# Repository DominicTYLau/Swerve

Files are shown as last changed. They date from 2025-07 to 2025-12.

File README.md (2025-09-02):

# Swerve

**Description:

** A swerve drivetrain completely 3D printed.

**Motivation for this project:** I wanted to make something similar to FRC swerve. I want to learn to program it.

Full CAD: https://a360.co/44cCmrA

## Demo:
https://youtube.com/shorts/nQBawvd5q3g?feature=share

## Pictures:
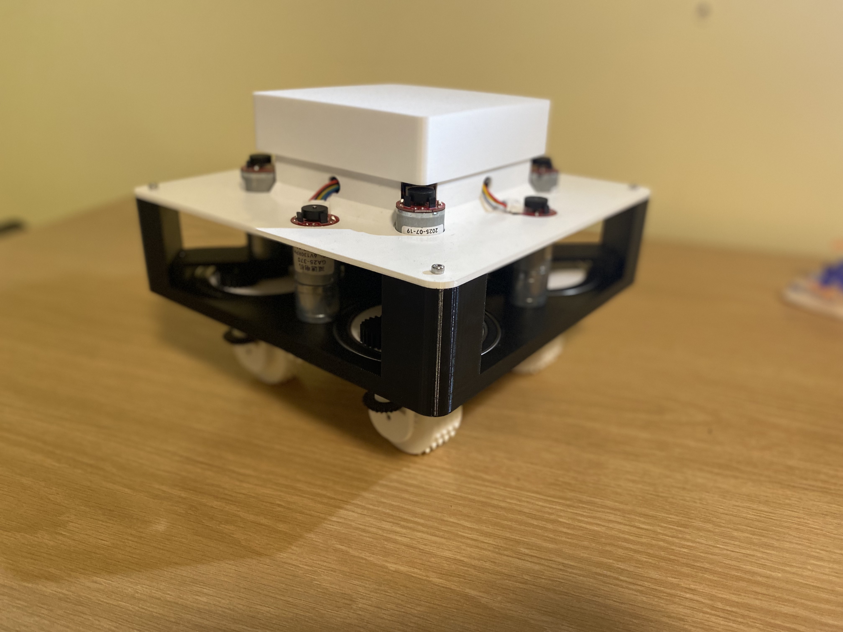
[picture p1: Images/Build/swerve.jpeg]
Swerve


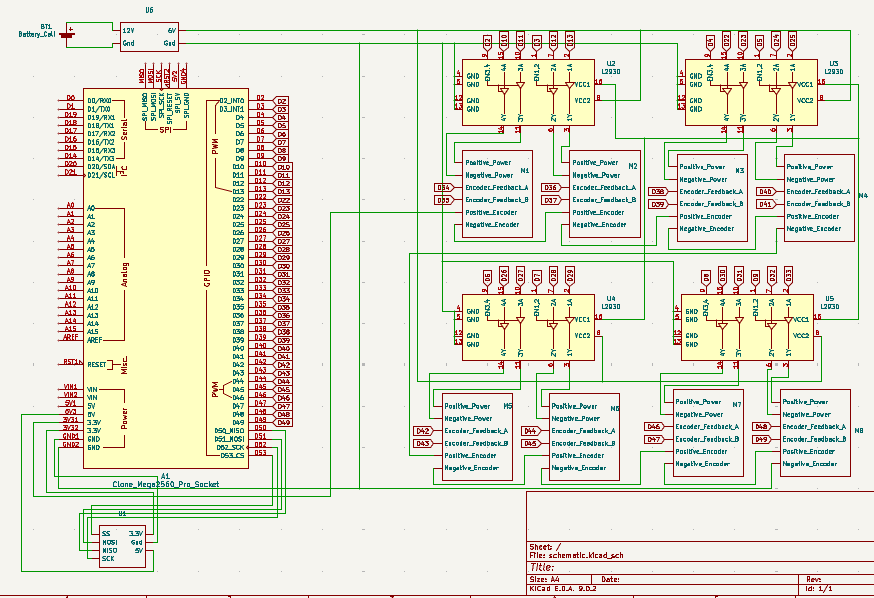
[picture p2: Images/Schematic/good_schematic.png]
Schematic


## BOM:

Purchase Items

| Item Name | What the Item Is For in Your Project | Item Source | Item Price (USD) | Quantity | Total Price (USD) | URL |
|---|---|---|---|---|---|-----|
| Geared Motors w/ encoders | One for steering motor and the other for drive motor. Four Wheels. | Aliexpress  | 10.93 | 8 | 87.44 | [Link](https://www.aliexpress.com/item/4001314473291.html) |
| M4 - 45 Hex Head Bolts | Transfer in power (check CAD) | Aliexpress  | 2.81 | 1 | 2.81 | [Link](https://www.aliexpress.com/item/32968601031.html) |
| Bearings | For rotation of each module | Aliexpress  | 13.29 | 2 | 26.58 | [Link](https://www.aliexpress.com/item/1005007420073930.html) |
| Arduino Mega | Need more ports | Amazon | 23.10 | 1 | 23.10 | [Link](https://www.amazon.ca/dp/B01H4ZLZLQ) |

**Total:** $149.96 USD

## Already Have

| Item | What the Item Is For in Your Project | Source  | Quantity | URL |
|---|---|---|---|-----|
| Lipo Battery | Power Robot | Amazon  | 1 | — |
| L293D | Motor Driver | Amazon  | 4 | — |
| M3 - 8mm Bolts  | — | Aliexpress | 1 | [Link](https://www.aliexpress.com/item/32810872544.html) |
| M4 - 40mm Bolts | — | Aliexpress | 1 | [Link](https://www.aliexpress.com/item/32810872544.html) |
| M3 - 4mm Bolts  | — | Aliexpress | 1 | [Link](https://www.aliexpress.com/item/32810872544.html) |
| ESP32  | — | Amazon | 1 | - |

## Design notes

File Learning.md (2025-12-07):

Each project allows me to grow. For this project, I learned:

* That the design and CAD phase is very important, as it saves a lot of time later on when building.
* To 3D print test pieces to avoid parts that don’t fit.
* To place the pinouts on the microcontroller near where they will be connected, making it easier to troubleshoot.
* That it is important to ensure the motors are receiving enough current.

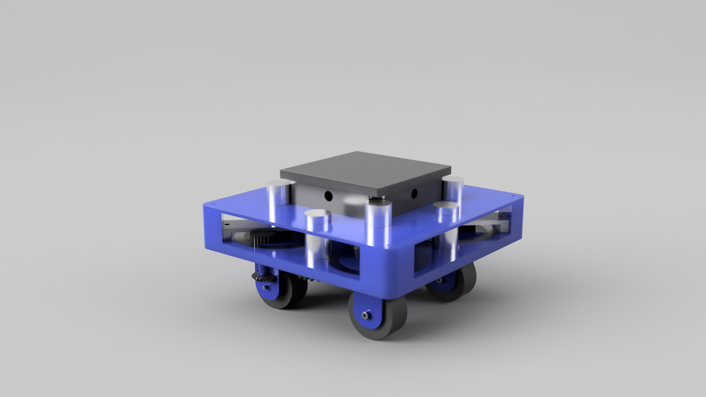
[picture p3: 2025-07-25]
Images/render.png

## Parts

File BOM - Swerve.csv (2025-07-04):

 |  |  |  | USD
Item name | What the item is for in your project | Item source | Item price (include taxes) | Quantity | Total Price (include shipping + taxes) | URL
Geared Motors w/ encoders | One for steering motor and the other for drive motor. Four Wheels. | Aliexpress | 10.93 | 8 | 87.44 | https://www.aliexpress.com/item/4001314473291.html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
Bluetooth Dongle | Connect game controller to control robot | Amazon | 2.77 | 1 | 2.77 | https://www.aliexpress.com/item/1005007299146273.html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
USB Host Shield | Connect USB to Arduino | Aliexpress | 4.34 | 1 | 4.34 | https://www.aliexpress.com/item/32817563853.html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 | Reference --> | https://www.amazon.ca/HiLetgo-Development-Compatible-Interface-Arduino/dp/B01EWW9R1E
IC Socket | Place for L293D to be placed so they can be resuable | Aliexpress | 2.92 | 1 | 2.92 | https://www.aliexpress.com/item/32863286734.html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
M4 - 45 Hex Head Bolts | To transfer power (check CAD) | Aliexpress | 2.81 | 1 | 2.81 | https://www.aliexpress.com/item/32968601031.html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
Bearings | For rotation of each module | Aliexpress | 13.29 | 2 | 26.58 | https://www.aliexpress.com/item/1005007420073930.html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
Arduino Mega | Need more ports | Amazon | 23.1 | 1 | 23.1 | https://www.amazon.ca/ELEGOO-Compatible-Arduino-Projects-Compliant/dp/B01H4ZLZLQ?s=industrial
 |  |  |  |  | 149.96
Already Have
Lipo Battery | Power Robot | Amazon
L293D | Motor Driver | Amazon
M3 - 8mm Bolts |  | Aliexpress | 2.36 | 1 | 2.36 | https://www.aliexpress.com/item/32810872544.html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
M4 - 40mm Bolts |  | Aliexpress | 4.34 | 1 | 4.34 | https://www.aliexpress.com/item/32810872544.html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
M3 - 4mm Bolts |  | Aliexpress | 1.94 | 1 | 1.94 | https://www.aliexpress.com/item/32810872544.html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

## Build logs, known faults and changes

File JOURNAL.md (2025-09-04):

---
title: "Swerve Bot"
author: "Dominic Lau"
description: "A swerve drivetrain that is 3D printed"
created_at: "2024-06-23"
---

Time Spent: 52 hours

# Planning & Designing

---

## June 23, 2025

New idea. Create a swerve drive that had odometry. I started by drawing different designs to see which ones were possible. I then did a simple cad to test if it would work. The cad took the longest because I had to figure out the best dimensions.

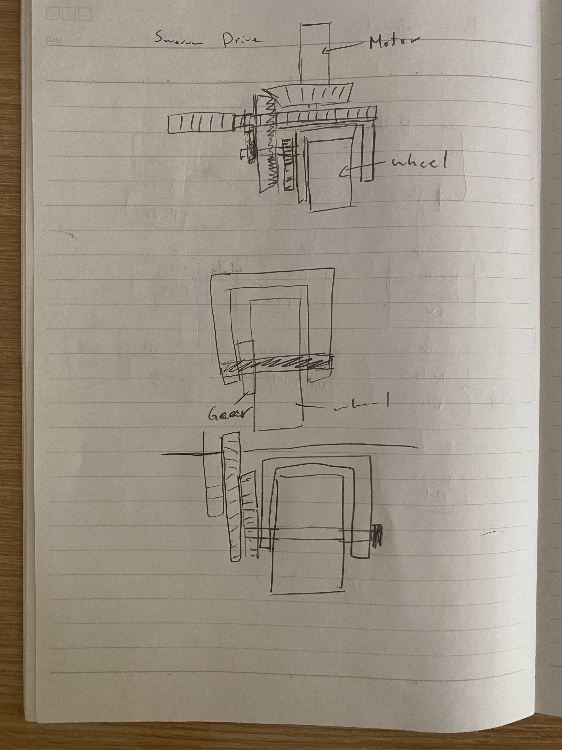
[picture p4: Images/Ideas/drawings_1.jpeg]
drawings_1

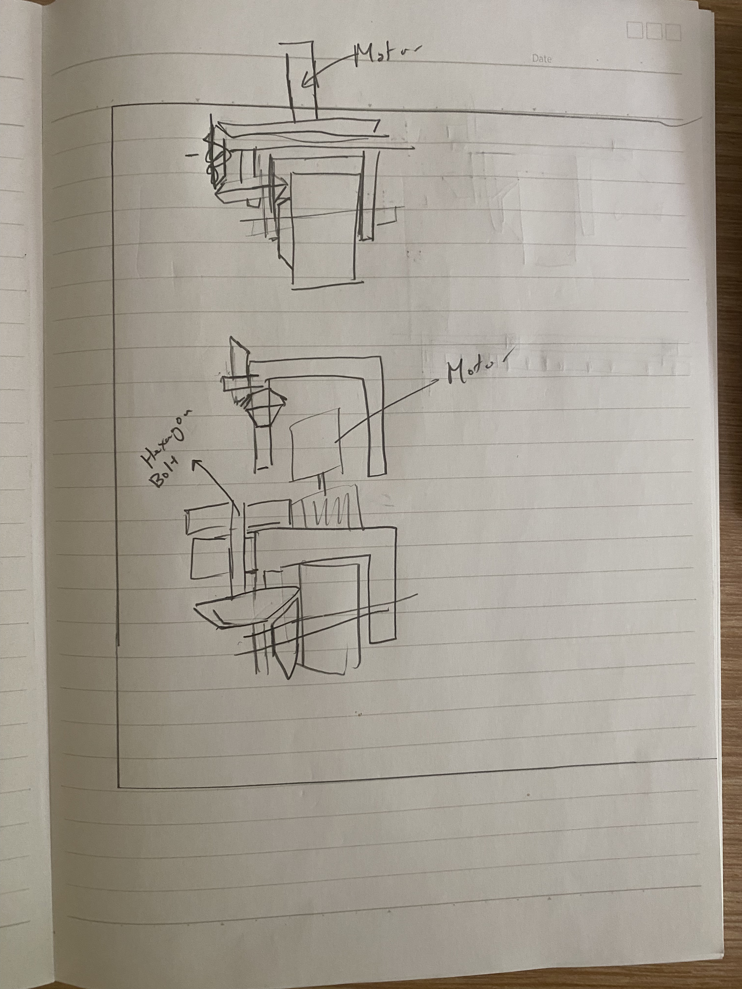
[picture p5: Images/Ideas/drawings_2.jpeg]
drawings_2

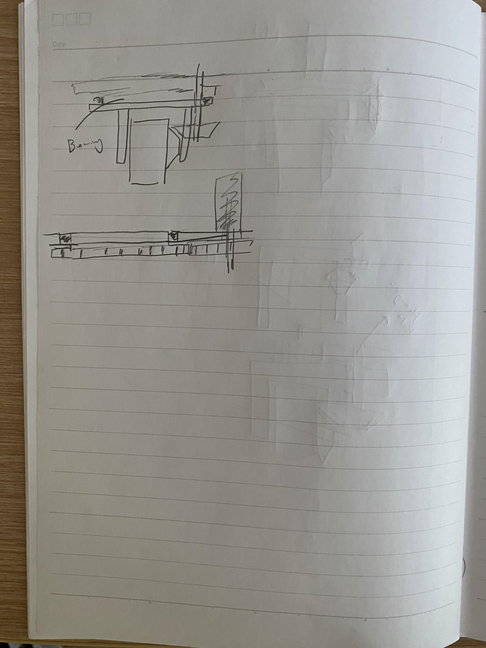
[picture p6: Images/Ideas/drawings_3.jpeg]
drawings_3


Time Spent: 1 hour

## June 24, 2025

I assembled the prototype. It worked pretty well. I had to fix some dimensions in the cad. I caded a bigger prototype that had more gears. I basically made one module of the swerve drivetrain. I also researched about the motors I was going to use. I wanted to have encoder to be more precise.

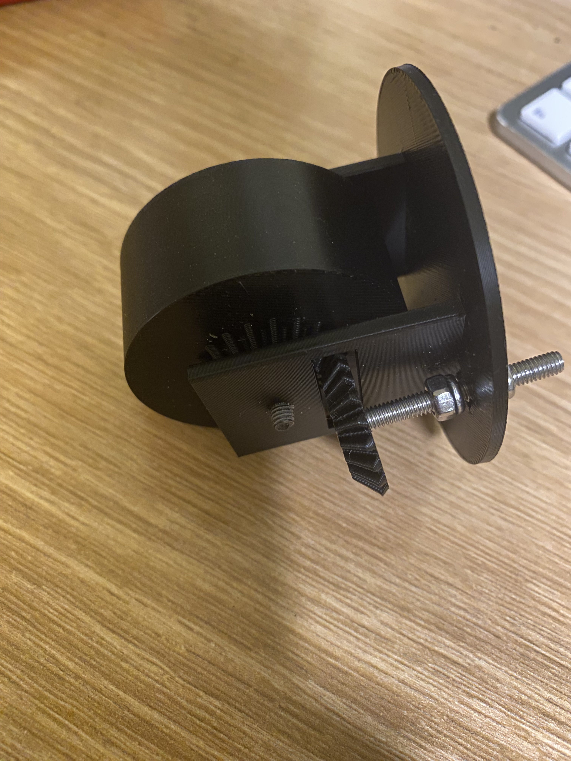
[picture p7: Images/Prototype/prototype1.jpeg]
prototype1


Time Spent: 2 hours

## June 25, 2025

I tested the second prototype and it worked pretty well. I spent the day cadding the whole robot. It took a lot of time trying to get all the joints working. The animations work and it looks pretty cool.

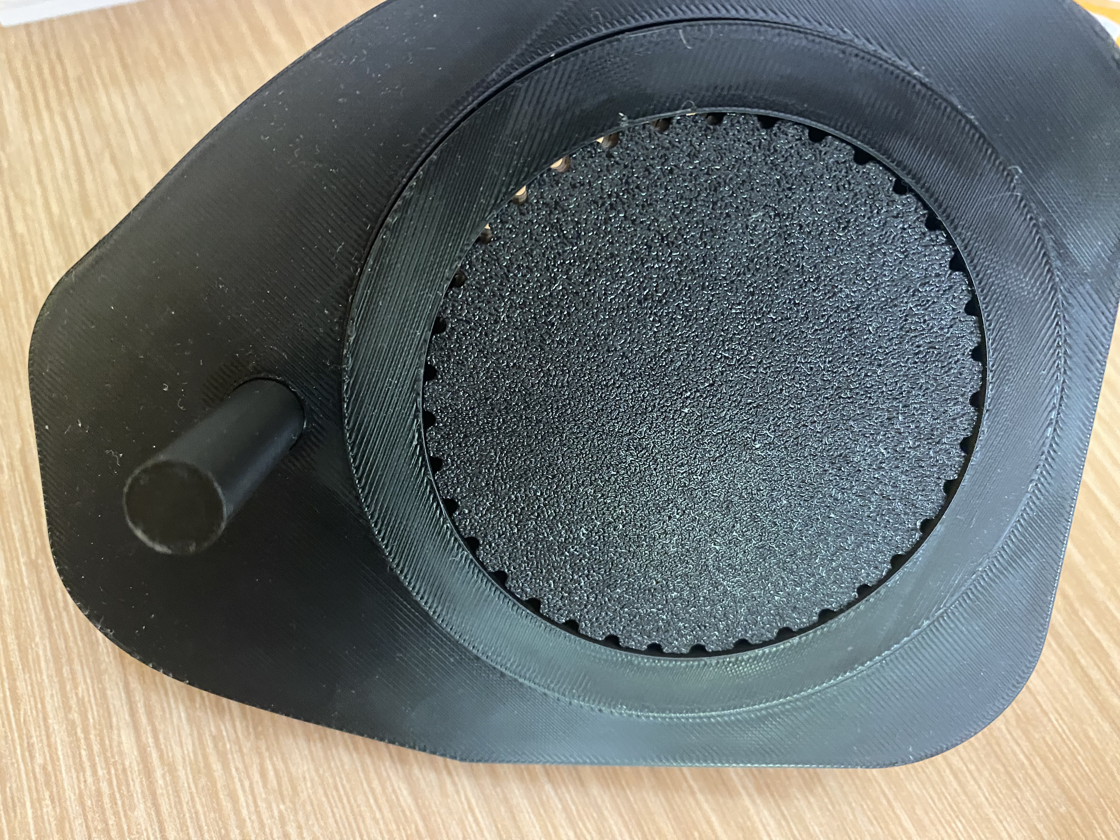
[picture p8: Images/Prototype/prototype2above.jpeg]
prototype2above

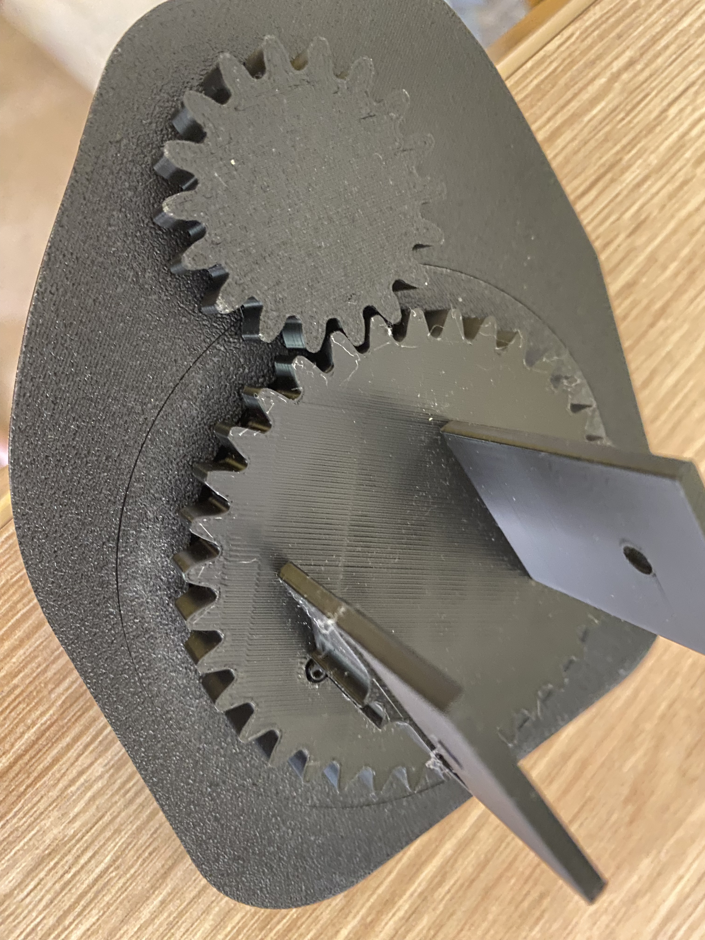
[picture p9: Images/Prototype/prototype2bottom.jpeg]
prototype2bottom

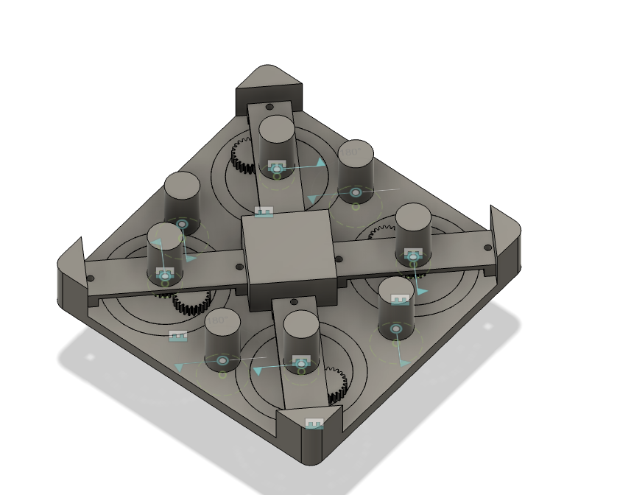
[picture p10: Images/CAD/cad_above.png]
cad_above

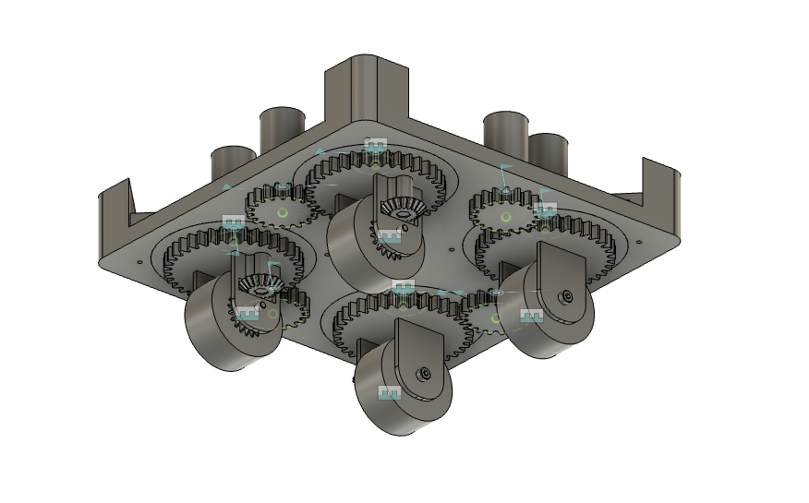
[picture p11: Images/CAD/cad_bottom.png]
cad_bottom

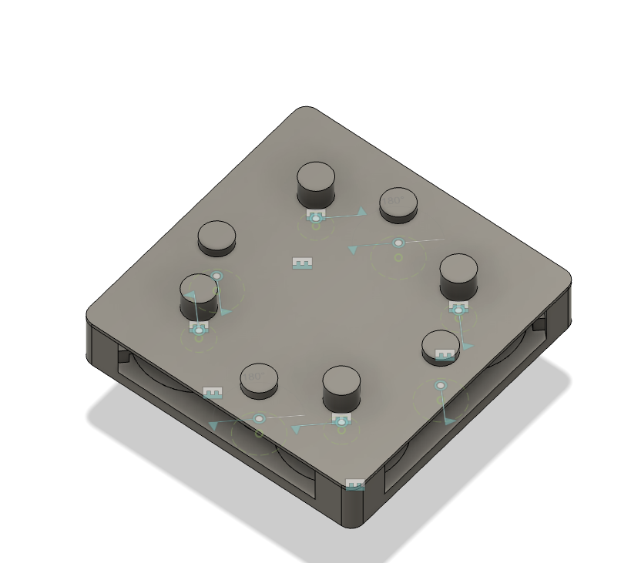
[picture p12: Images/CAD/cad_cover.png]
cad_cover

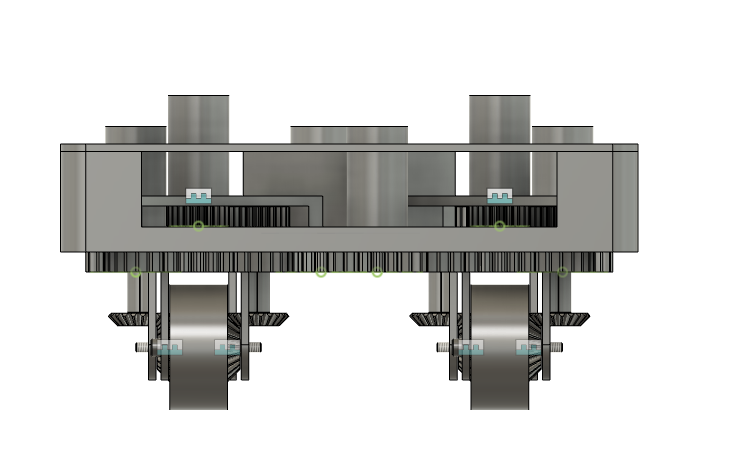
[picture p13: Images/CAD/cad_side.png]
cad_side


Time Spent: 5 hours

## June 26, 2025

I now focused more on the electronics. I started off my listing the BOM. Then, I made a power distribution diagram with the control diagram.

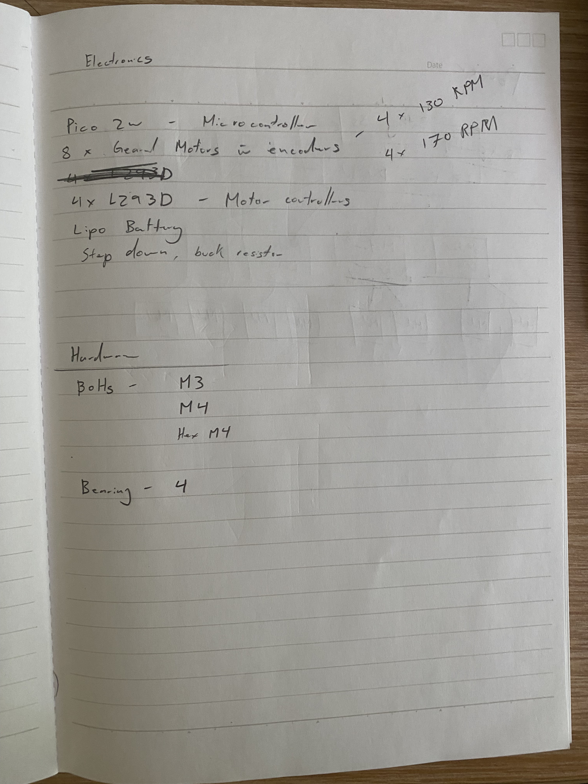
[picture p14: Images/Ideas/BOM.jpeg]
BOM

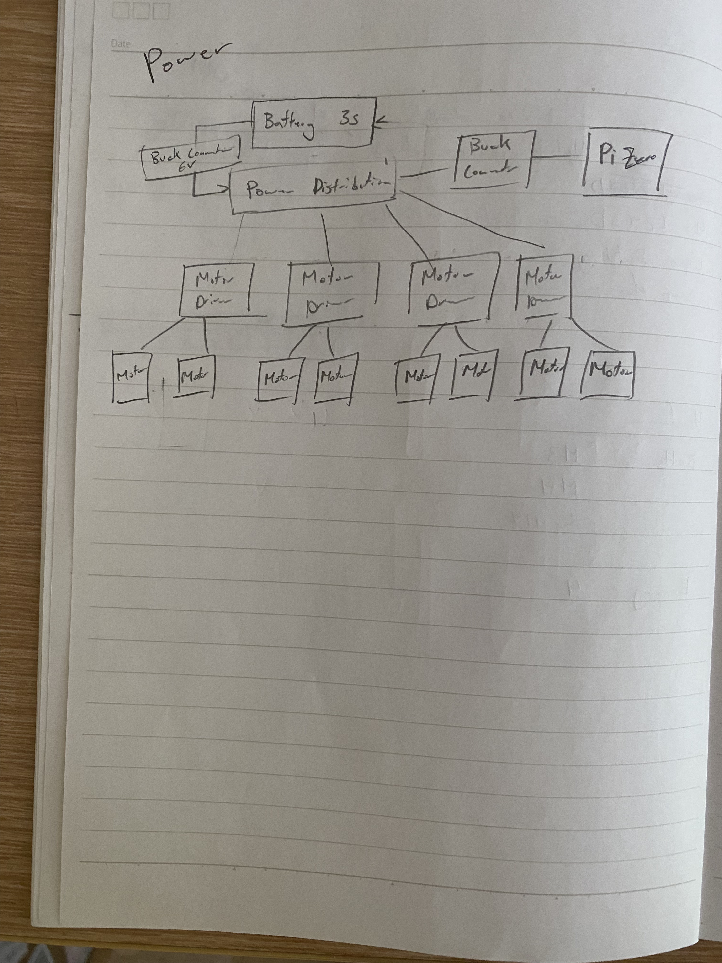
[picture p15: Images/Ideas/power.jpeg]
power

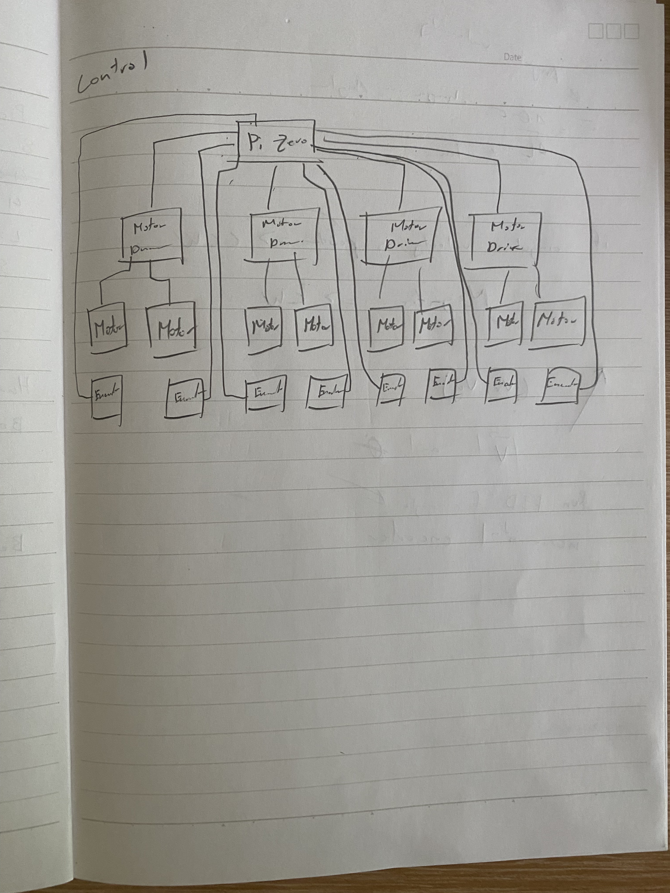
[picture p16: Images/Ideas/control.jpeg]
control


Time Spent: 1 hour

## June 27, 2025

I moved on to doing the schematic. I made the necessary symbols then started wiring the whole robot. Halfway through, I realized that the raspberry pi zero did not have enough GPIO pins so I had to switch to Arduino mega. This took way too long but it was needed to be done.

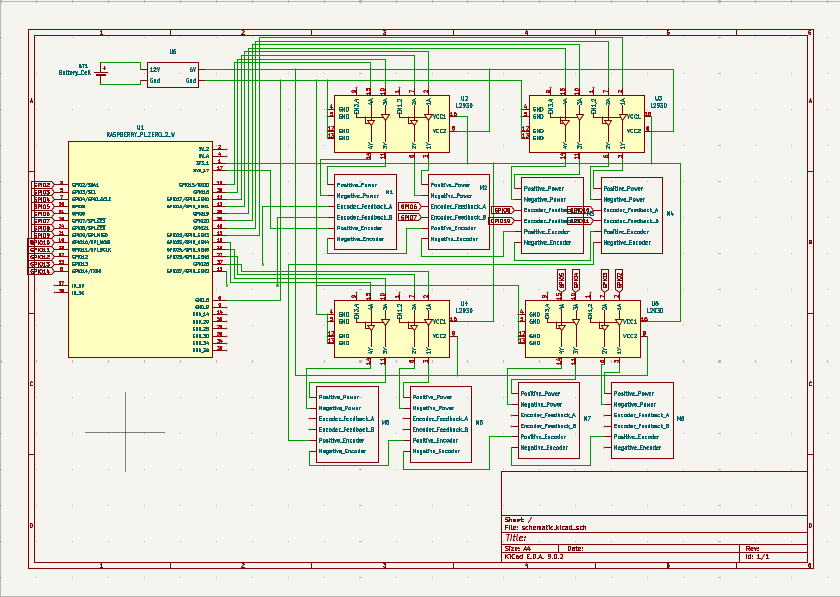
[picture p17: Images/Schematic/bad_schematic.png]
bad_schematic

good_schematic

Time Spent: 3 hours

## June 28, 2025

Next, I went to the programming phase. I started by doing research and found this article. This gave me a fundamental understanding. Essentially, I have to add vectors. Finally an application of vectors. https://dominik.win/blog/programming-swerve-drive/

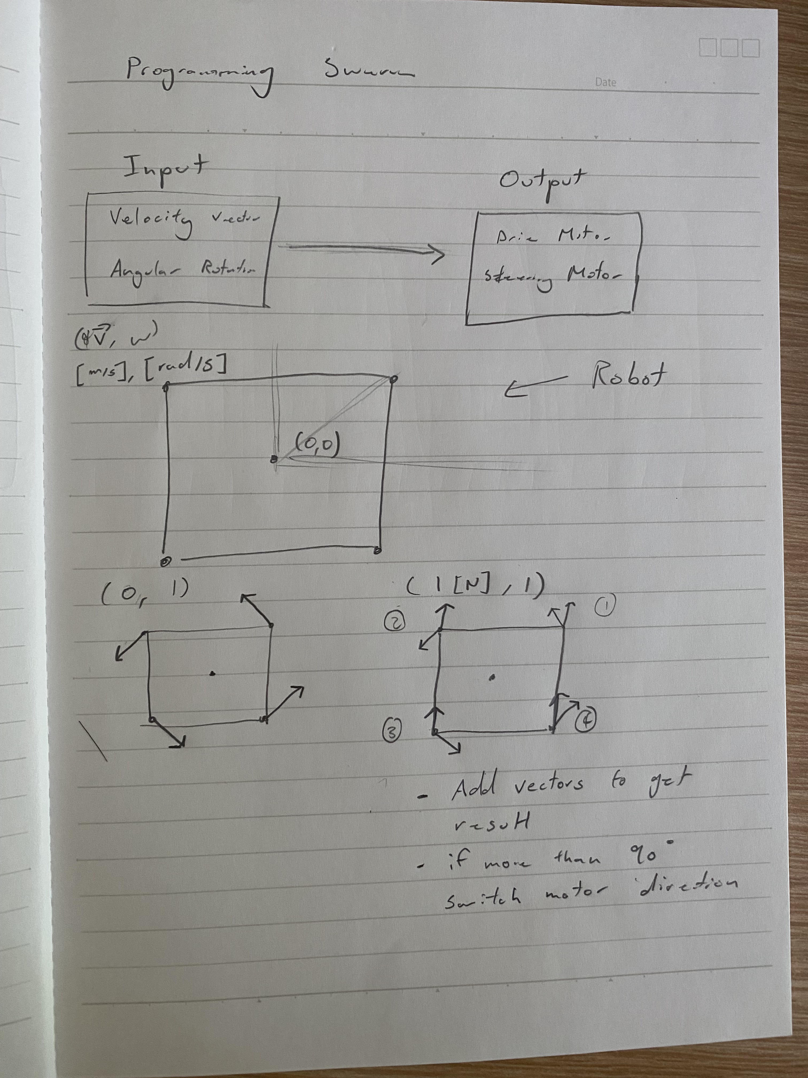
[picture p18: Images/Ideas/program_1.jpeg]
program_1

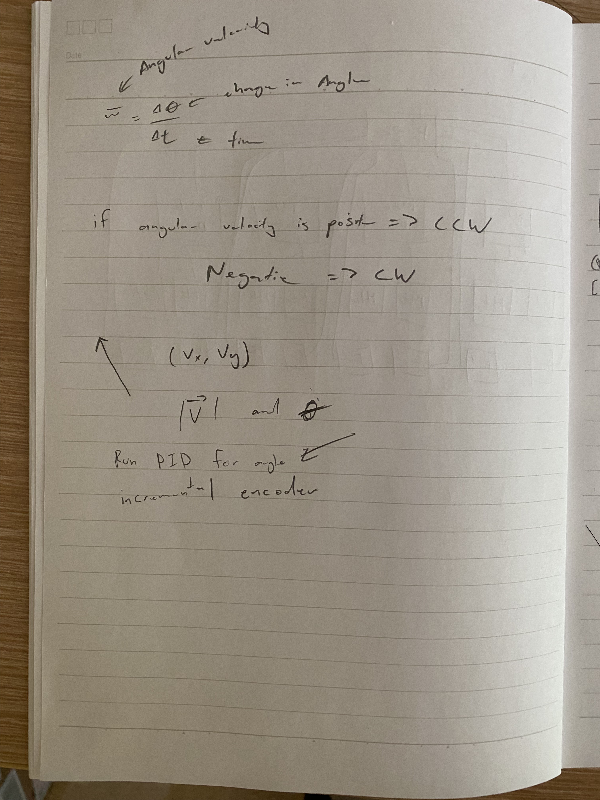
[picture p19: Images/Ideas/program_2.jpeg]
program_2


Time Spent: 2 hours

## July 1, 2025

The code is very long. I first declared all the electronics that were connected to the arduino mega. I then figured out how to add the vectors and make it have magnitude and direction. I then learned to use pid for the turning of each module. Lastly, I researched the code for using a ps4 controller to connect. 

Here are the sources I used:

https://github.com/PaulStoffregen/Encoder/blob/master/examples/Basic/Basic.ino
https://github.com/PowerBroker2/ArduPID/blob/main/examples/example/example.ino
http://brettbeauregard.com/blog/2011/04/improving-the-beginners-pid-introduction/
https://lastminuteengineers.com/l293d-dc-motor-arduino-tutorial/
https://maker.pro/arduino/projects/how-to-control-an-arduino-robot-with-a-ps4-bluetooth-controller

Time Spent: 5 hours

## Jun 21, 2025

I finalized the BOM and wrote the README.md

Time Spent: 1 hour 

---

# Build

## Aug 9, 2025

I got most of the parts that I ordered so I can start 3D printing. I started by printing small parts to test the tolerance for each part. It took many tries to get it perfect.

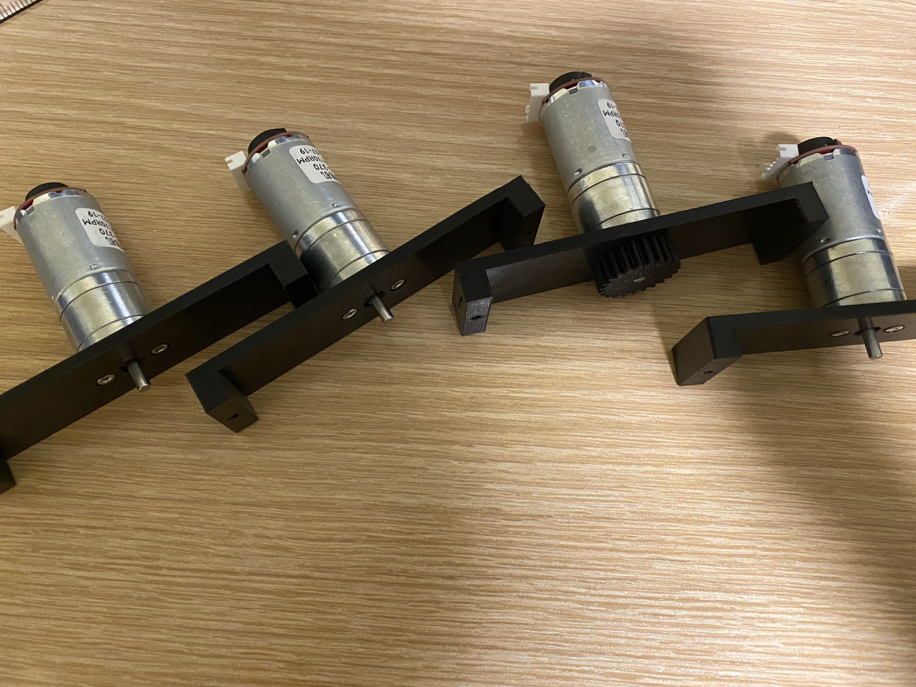
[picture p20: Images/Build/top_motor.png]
top


Time Spent: 2 hours

## Aug 10, 2025

I continued to print the base and drivetrain. I then assembled the parts that was ready.

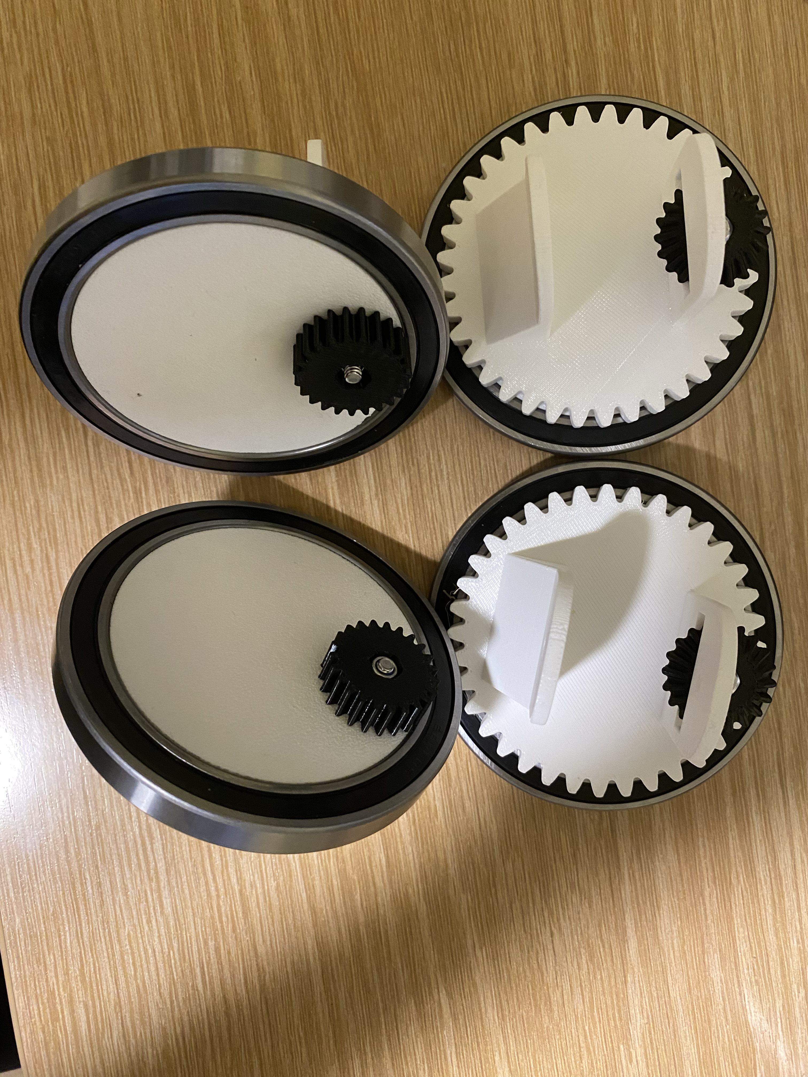
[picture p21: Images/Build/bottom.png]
bottom


Time Spent: 2 hours

## Aug 11, 2025

I continued to print the base and drivetrain. I assembled everything and it looks amazing.

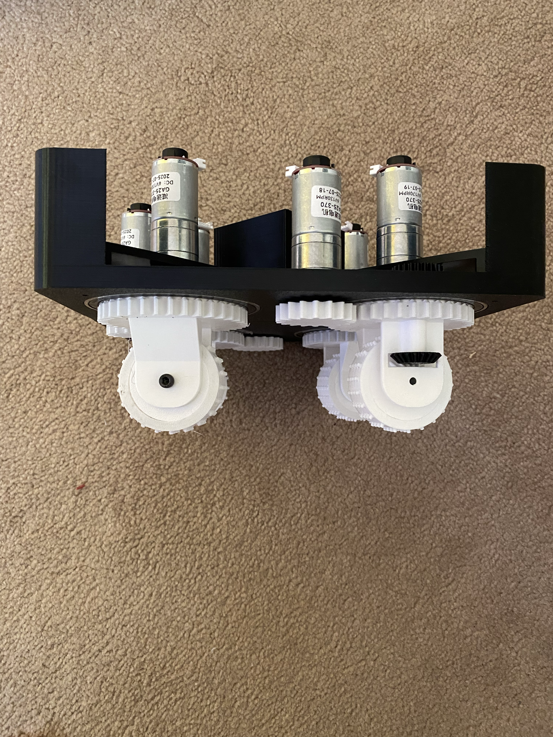
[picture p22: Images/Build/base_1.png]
base_1

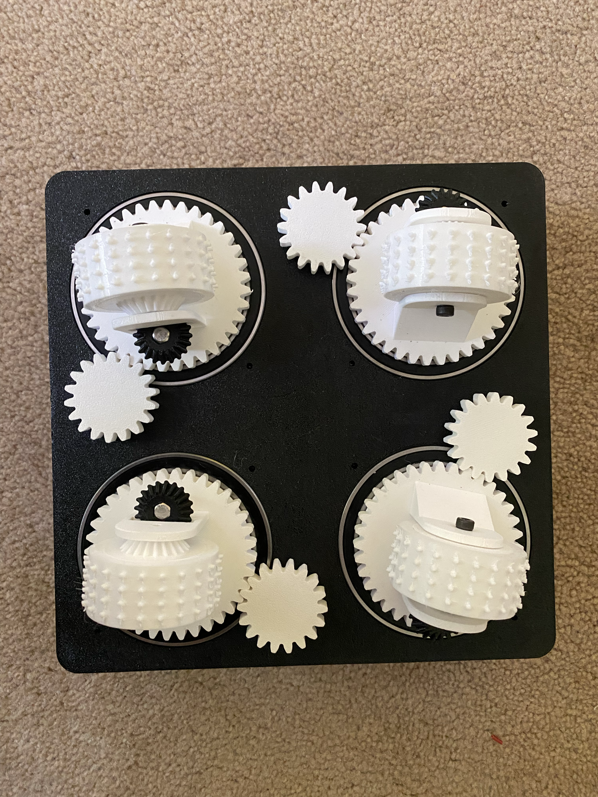
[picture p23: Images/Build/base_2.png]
base_2

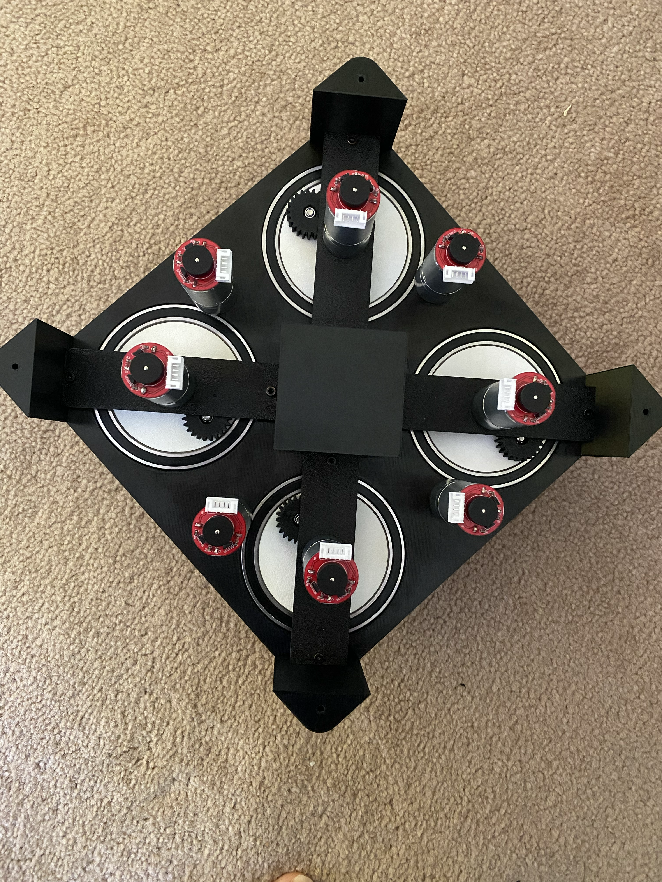
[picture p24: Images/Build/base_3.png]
base_3


Time Spent: 1 hour

Please note that the photos were taken after I completed the work, and the journal was written afterward. Some parts of the project may have carried over across multiple days. The recorded times are not entirely accurate... I actually spent more time, but noted conservative estimates.

## Aug 18, 2025

I received the Arduino Mega, but it did not when the code was uploaded. I tried to find if there was a mode for flashing but nothing worked. I ordered a new one off of amazon this time. Hopefully more reliable.

Time Spent: 2 hours

## Aug 25, 2025

I received the new Arduino Mega and it worked great. Blink worked which was a relief. I soldered on some connectors for the motor pins so that they would fit the arduino pins and not come out. This took very long as there were 6 wires each for one motor, and I had to solder for 8 motors. I started wiring everything which was a pain.

Time Spent: 7 hours

## Aug 26, 2025

I ran some simple code to see if it would work. However, some of the motors worked while others didn’t. I figured out that I wired it incorrectly. I realized that it was going to be a diagnose later because the pins on the arduino mega and the motor controllers were very far from each other. I rewired it so that it would be easier to trouble shoot.

Time Spent: 5 hours

## Aug 27, 2025

I ran some basic code to run all the motors which worked great. Then I started to control the angle of the steering. However, PID did not work as only a selected few ports on the mega had pwm output. I then resorted to bang bang control which worked good enough. I then combined everything and that was when it didn’t work. After testing once, some of the motors stopped working. I spent the next 2 hours testing each module. I found that the wires were a problem and they were unreliable. I made my own wires and rewired everything. I tested each mother and it worked.

Time Spent: 8 hours

## Aug 28, 2025

Now that the motors were reliable, I could test my code once again and debug. It took some time, but overall it works really well.

Time Spent: 4 hours

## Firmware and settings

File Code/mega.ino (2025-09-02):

#include <PinChangeInterrupt.h>
#include <math.h>

// -------------------- Motor Pins --------------------
// Steering motors
#define motor_1_en 8
#define motor_1_in_A 9
#define motor_1_in_B 31

#define motor_3_en 25
#define motor_3_in_A 26
#define motor_3_in_B 27

#define motor_5_en 38
#define motor_5_in_A 39
#define motor_5_in_B 40

#define motor_7_en 2
#define motor_7_in_A 3
#define motor_7_in_B 4

// Drive motors
#define motor_2_en 28
#define motor_2_in_A 29
#define motor_2_in_B 30

#define motor_4_en 22
#define motor_4_in_A 23
#define motor_4_in_B 24

#define motor_6_en 41
#define motor_6_in_A 42
#define motor_6_in_B 43

#define motor_8_en 5
#define motor_8_in_A 6
#define motor_8_in_B 7

// -------------------- Encoder Pins --------------------
#define ENC1_A 10
#define ENC1_B 11
#define ENC3_A 50
#define ENC3_B 51
#define ENC5_A 52
#define ENC5_B 53
#define ENC7_A 12
#define ENC7_B 13

volatile long encoder1Count = 0;
volatile long encoder3Count = 0;
volatile long encoder5Count = 0;
volatile long encoder7Count = 0;

// -------------------- Encoder Constants --------------------
const float COUNTS_PER_REV = 1970.0;
const float DEG_PER_COUNT = 360.0 / COUNTS_PER_REV;

// -------------------- Robot Geometry --------------------
const float WHEELBASE = 0.12; // meters
const float TRACKWIDTH = 0.12; // meters

// wheel positions relative to robot center
const float wheelX[4] = { WHEELBASE/2,  WHEELBASE/2, -WHEELBASE/2, -WHEELBASE/2 };
const float wheelY[4] = { TRACKWIDTH/2, -TRACKWIDTH/2, -TRACKWIDTH/2,  TRACKWIDTH/2 };

// -------------------- Control --------------------
const float deadzone = 8.0;

// -------------------- Helper Functions --------------------
float countsToDegrees(long counts) {
  float deg = counts * DEG_PER_COUNT;
  deg = fmod(deg, 360.0);
  if (deg < 0) deg += 360.0;
  return deg;
}

float closestAngle(float current, float target) {
  float delta = fmod(target - current + 540.0, 360.0) - 180.0;
  return delta;
}

void setSteeringMotor(int en, int inA, int inB, float errorDeg) {
  if (errorDeg > deadzone) {
    digitalWrite(inA, HIGH); digitalWrite(inB, LOW);
    analogWrite(en, 255);
  } else if (errorDeg < -deadzone) {
    digitalWrite(inA, LOW); digitalWrite(inB, HIGH);
    analogWrite(en, 255);
  } else {
    digitalWrite(inA, LOW); digitalWrite(inB, LOW);
    analogWrite(en, 0);
  }
}

void setDriveMotor(int en, int inA, int inB, float speed) {
  int pwm = constrain(abs(speed) * 255, 0, 255);
  if (speed > 0) {
    digitalWrite(inA, HIGH); digitalWrite(inB, LOW);
  } else if (speed < 0) {
    digitalWrite(inA, LOW); digitalWrite(inB, HIGH);
  } else {
    digitalWrite(inA, LOW); digitalWrite(inB, LOW);
  }
  analogWrite(en, pwm);
}

void optimizeAngle(float &targetAngle, float &wheelSpeed, float currentAngle) {
  float delta = closestAngle(currentAngle, targetAngle);
  if (delta > 90.0) {
    targetAngle = fmod(targetAngle + 180.0, 360.0);
    wheelSpeed *= -1;
  } else if (delta < -90.0) {
    targetAngle = fmod(targetAngle - 180.0, 360.0);
    wheelSpeed *= -1;
  }
}

// -------------------- Encoder ISR --------------------
void encoder1ISR() { if (digitalRead(ENC1_A) == digitalRead(ENC1_B)) encoder1Count++; else encoder1Count--; }
void encoder3ISR() { if (digitalRead(ENC3_A) == digitalRead(ENC3_B)) encoder3Count++; else encoder3Count--; }
void encoder5ISR() { if (digitalRead(ENC5_A) == digitalRead(ENC5_B)) encoder5Count++; else encoder5Count--; }
void encoder7ISR() { if (digitalRead(ENC7_A) == digitalRead(ENC7_B)) encoder7Count++; else encoder7Count--; }

// -------------------- Setup --------------------
void setup() {
  Serial.begin(115200);
  Serial1.begin(115200);

  int motorPins[] = {motor_1_en, motor_1_in_A, motor_1_in_B,
                     motor_2_en, motor_2_in_A, motor_2_in_B,
                     motor_3_en, motor_3_in_A, motor_3_in_B,
                     motor_4_en, motor_4_in_A, motor_4_in_B,
                     motor_5_en, motor_5_in_A, motor_5_in_B,
                     motor_6_en, motor_6_in_A, motor_6_in_B,
                     motor_7_en, motor_7_in_A, motor_7_in_B,
                     motor_8_en, motor_8_in_A, motor_8_in_B};
  for (int i=0; i<24; i++) pinMode(motorPins[i], OUTPUT);

  pinMode(ENC1_A, INPUT_PULLUP); pinMode(ENC1_B, INPUT_PULLUP);
  pinMode(ENC3_A, INPUT_PULLUP); pinMode(ENC3_B, INPUT_PULLUP);
  pinMode(ENC5_A, INPUT_PULLUP); pinMode(ENC5_B, INPUT_PULLUP);
  pinMode(ENC7_A, INPUT_PULLUP); pinMode(ENC7_B, INPUT_PULLUP);

  attachPinChangeInterrupt(digitalPinToPinChangeInterrupt(ENC1_A), encoder1ISR, CHANGE);
  attachPinChangeInterrupt(digitalPinToPinChangeInterrupt(ENC3_A), encoder3ISR, CHANGE);
  attachPinChangeInterrupt(digitalPinToPinChangeInterrupt(ENC5_A), encoder5ISR, CHANGE);
  attachPinChangeInterrupt(digitalPinToPinChangeInterrupt(ENC7_A), encoder7ISR, CHANGE);

  Serial.println("Swerve Drive Ready");
}

// -------------------- Loop --------------------
void loop() {
  static String input = "";
  while (Serial1.available()) {
    char c = Serial1.read();
    if (c == '\n') {
      int Lx, Ly, Rx;
      sscanf(input.c_str(), "%d,%d,%d", &Lx, &Ly, &Rx);
      input = "";

      float x = Lx / 127.0;
      float y = -Ly / 127.0;
      float rot = Rx / 127.0;

      float wheelSpeeds[4];
      float wheelAngles[4];

      if (fabs(x) < 0.05 && fabs(y) < 0.05 && fabs(rot) > 0.05) {
        // --- Pure rotation in place ---
        // wheels face tangent to circle: 45, 135, 225, 315
        wheelAngles[0] = 135;   wheelSpeeds[0] = fabs(rot);
        wheelAngles[1] = 45;  wheelSpeeds[1] = fabs(rot);
        wheelAngles[2] = 315;  wheelSpeeds[2] = fabs(rot);
        wheelAngles[3] = 225;  wheelSpeeds[3] = fabs(rot);


        // direction based on sign of rot
        if (rot < 0) {
          for (int i=0; i<4; i++) wheelSpeeds[i] *= -1; // CW
        }

      } else {
        // --- Normal swerve math ---
        for (int i=0; i<4; i++) {
          float vx = x + (-rot * wheelY[i]);
          float vy = y + ( rot * wheelX[i]);
          wheelSpeeds[i] = sqrt(vx*vx + vy*vy);
          wheelAngles[i] = atan2(vy, vx) * 180.0 / M_PI;
          if (wheelAngles[i] < 0) wheelAngles[i] += 360.0;
        }
        float maxWs = max(max(wheelSpeeds[0], wheelSpeeds[1]), max(wheelSpeeds[2], wheelSpeeds[3]));
        if (maxWs > 1.0) for (int i=0; i<4; i++) wheelSpeeds[i] /= maxWs;
      }

      float current[4] = {
        countsToDegrees(encoder1Count),
        countsToDegrees(encoder3Count),
        countsToDegrees(encoder5Count),
        countsToDegrees(encoder7Count)
      };

      for (int i=0; i<4; i++) optimizeAngle(wheelAngles[i], wheelSpeeds[i], current[i]);

      float err1 = closestAngle(current[0], wheelAngles[0]);
      float err3 = closestAngle(current[1], wheelAngles[1]);
      float err5 = closestAngle(current[2], wheelAngles[2]);
      float err7 = closestAngle(current[3], wheelAngles[3]);

      setSteeringMotor(motor_1_en, motor_1_in_A, motor_1_in_B, err1);
      setSteeringMotor(motor_3_en, motor_3_in_A, motor_3_in_B, err3);
      setSteeringMotor(motor_5_en, motor_5_in_A, motor_5_in_B, err5);
      setSteeringMotor(motor_7_en, motor_7_in_A, motor_7_in_B, err7);

      setDriveMotor(motor_2_en, motor_2_in_A, motor_2_in_B, wheelSpeeds[0]);
      setDriveMotor(motor_4_en, motor_4_in_A, motor_4_in_B, wheelSpeeds[1]);
      setDriveMotor(motor_6_en, motor_6_in_A, motor_6_in_B, wheelSpeeds[2]);
      setDriveMotor(motor_8_en, motor_8_in_A, motor_8_in_B, wheelSpeeds[3]);

      Serial.print("Angles: ");
      for (int i=0; i<4; i++) {
        Serial.print(wheelAngles[i]); Serial.print(", ");
      }
      Serial.println();
    } else {
      input += c;
    }
  }
}

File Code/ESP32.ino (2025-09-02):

// ESP32-WROOM-32 DevKit v1
// Code: Receive PS4 controller input and send via UART to Arduino

#include <PS4Controller.h>

unsigned long lastTimeStamp = 0;
const int DEADZONE = 15; // adjust as needed (0–127 range per axis)

int applyDeadzone(int value) {
  if (abs(value) < DEADZONE) {
    return 0;
  }
  return value;
}

void notify() {
  // Apply deadzone to joystick values
  int lx = applyDeadzone(PS4.LStickX());
  int ly = applyDeadzone(PS4.LStickY());
  int rx = applyDeadzone(PS4.RStickX());

  // Format joystick values into CSV string
  char messageString[100];
  sprintf(messageString, "%d,%d,%d\n", lx, ly, rx);

  // Send every 50 ms
  if (millis() - lastTimeStamp > 50) {
    Serial2.print(messageString);   // TX2 (GPIO17) → Arduino Mega RX1
    lastTimeStamp = millis();
  }
}

void onConnect() {
  Serial.println("PS4 Controller Connected!");
}

void onDisConnect() {
  Serial.println("PS4 Controller Disconnected!");
}

void setup() {
  Serial.begin(115200);     // Debug output
  Serial2.begin(115200, SERIAL_8N1, 16, 17); // RX=16, TX=17 explicitly

  PS4.attach(notify);
  PS4.attachOnConnect(onConnect);
  PS4.attachOnDisconnect(onDisConnect);

  PS4.begin();  // Starts Bluetooth pairing
  Serial.println("ESP32 Ready. Waiting for PS4 controller...");
}

void loop() {
  // Empty loop, everything handled by callbacks
}
